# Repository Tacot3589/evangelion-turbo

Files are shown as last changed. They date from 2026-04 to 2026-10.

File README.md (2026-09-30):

# *Big thanks to those who helped make this project possible:*

<p align="center">
  <a href="https://roboilo.com/">
    RoboIlo
  </a>
</p>

<p align="center">
  <a href="https://www.pcbway.com/">
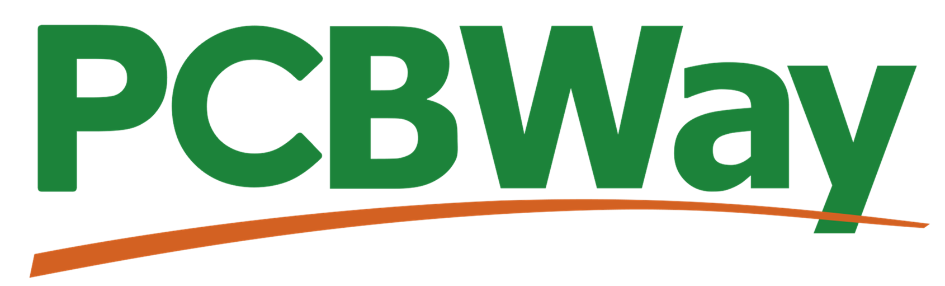
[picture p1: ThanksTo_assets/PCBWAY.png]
PCBWay
    
  </a>
  &nbsp;&nbsp;&nbsp;
  <a href="https://www.rosa3d.pl/en/">
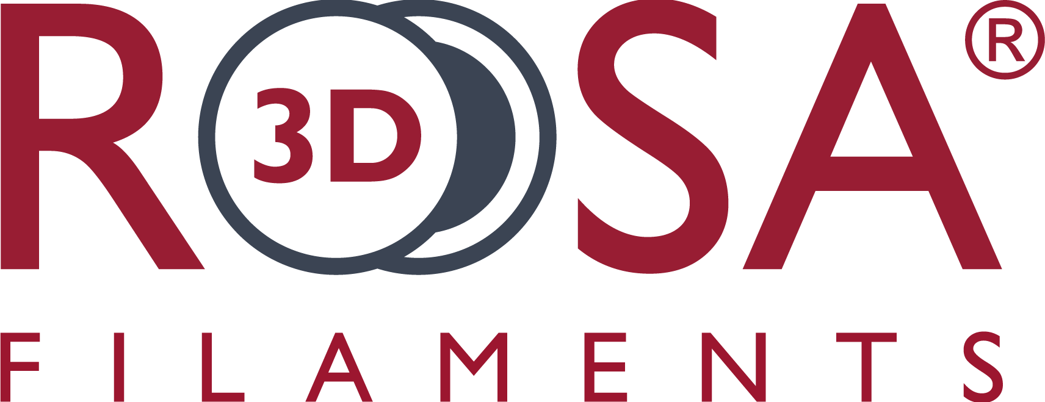
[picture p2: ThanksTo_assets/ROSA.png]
Rosa3D
    
  </a>
</p>

<p align="center">
  <a href="https://forge.hackclub.com/auth/hca/start?ref=7YQKYFS7">
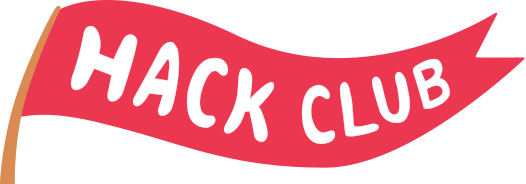
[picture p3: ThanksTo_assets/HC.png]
Hack Club: Forge
    
  </a>
  <a href="https://hackclub.com/">
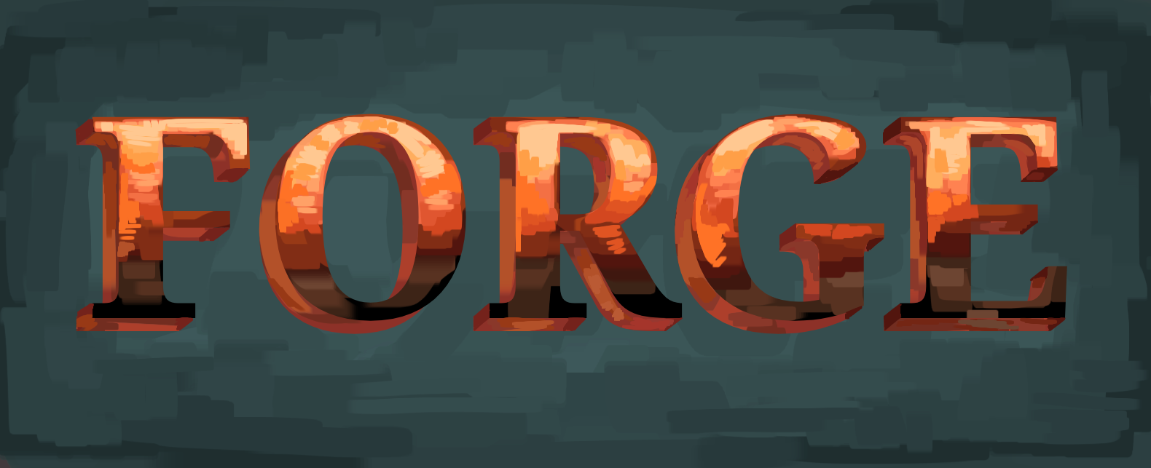
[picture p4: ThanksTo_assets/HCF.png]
Hack Club
    
  </a>
</p>

<p align="center">
  <a href="https://www.omc-stepperonline.com/">
    OMC StepperOnline
  </a>
</p>

---

# Evangelion turbo - my biggest project and most complicated robot yet - succesor to Evangelion
Sumo robot build by me! Designed for RoboRave competition 2026
- 10x10cm robot footprint (max 18-25cm, i think about adding flags)
- max 1kg
- Parts manufactured from steel, aluminium and high performance filaments
- 4 Distance sensors 
- 4 line sensors
- IMU
- shielded motors
- EPROM memory on board
- strong and fast stm32H5 mcu
- 7.5 gear ratio
- powerfull external mosfters motor drivers capable of high current
- two high power brushed DC motors

#### Pros:
 - powerfull motors
 - Capable motors drivers
 - Fast sensors
 - Capable MCU

#### Cons:
 - In the first version, the IMU refused to function (messed up SCL and SDA in I2C)
 - The mighty torque of the motors caused the front to rise, thereby troubling the sensors :(

#### Accomplishments:
 - "RoboRave Robotics Championship 2026 Osaka"

# Photos and images:

## 3D Model:
<p align="center">
  <a>
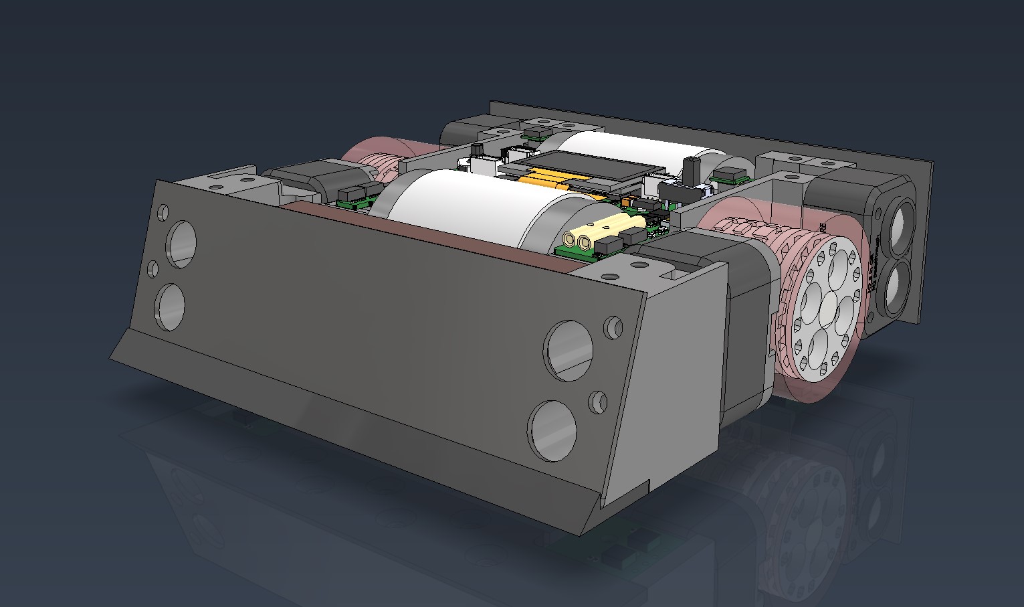
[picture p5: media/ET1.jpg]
ET1
    
  </a>
  <a>
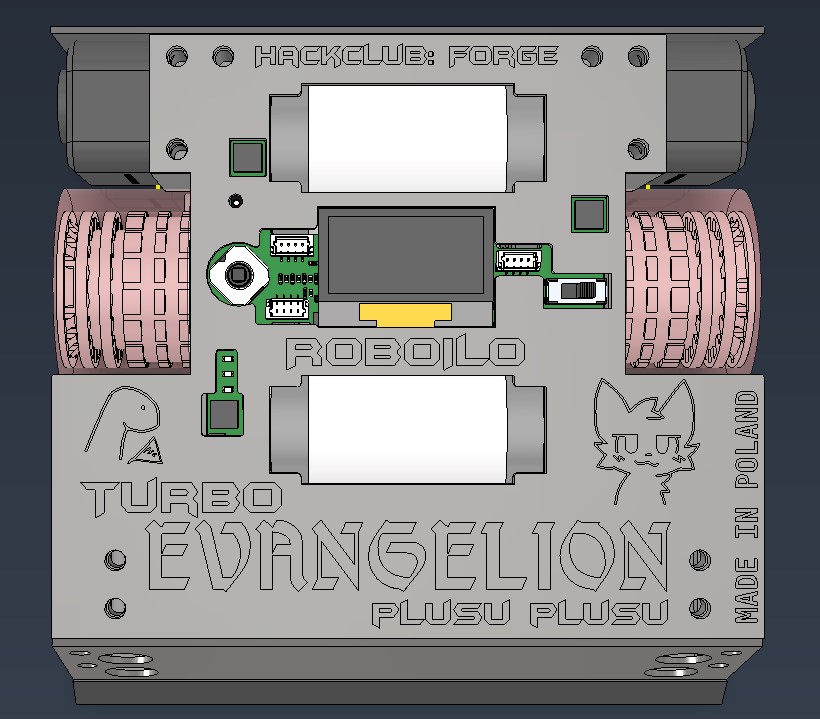
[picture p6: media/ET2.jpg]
ET2
    
  </a>
</p>
<p align="center">
  <a>
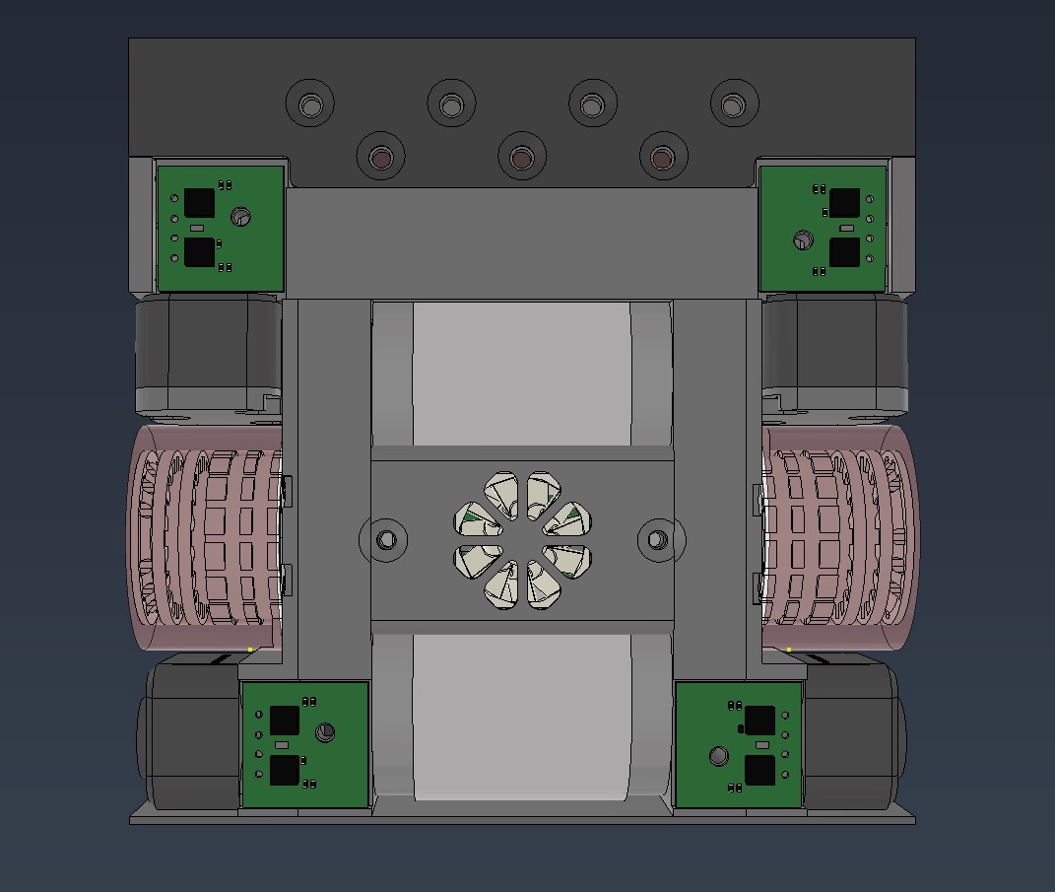
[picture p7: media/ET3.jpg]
ET3
    
  </a>
  <a>
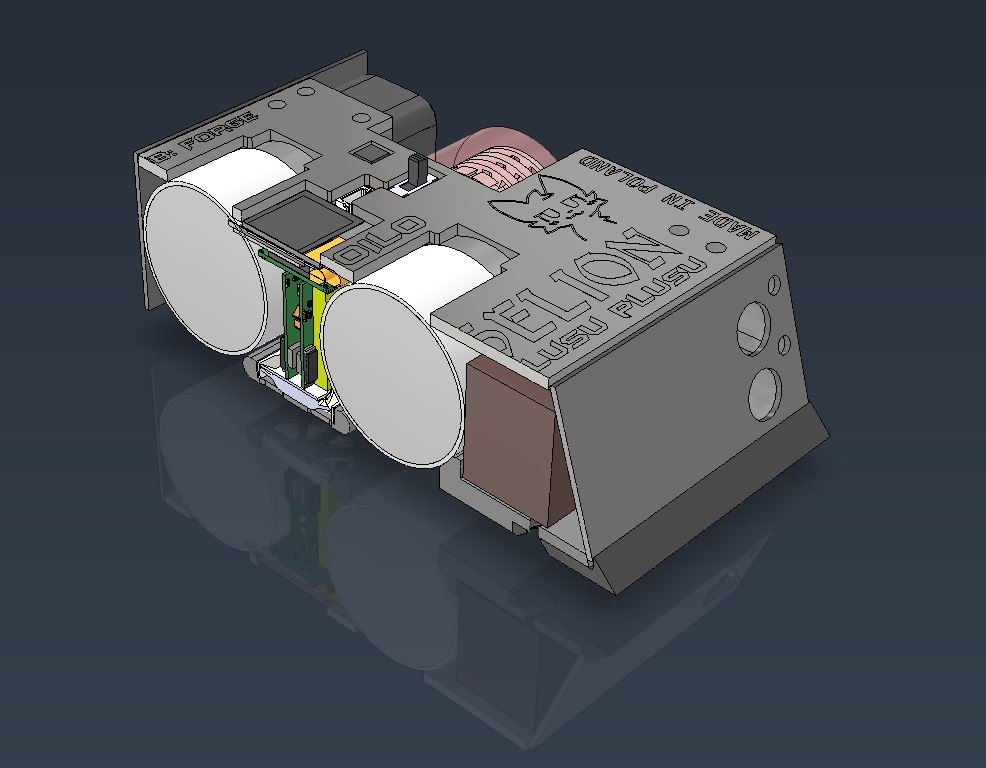
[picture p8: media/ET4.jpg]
ET4
    
  </a>
</p>

## Main controller (4 layer PCB):
<p align="center">
  <a>
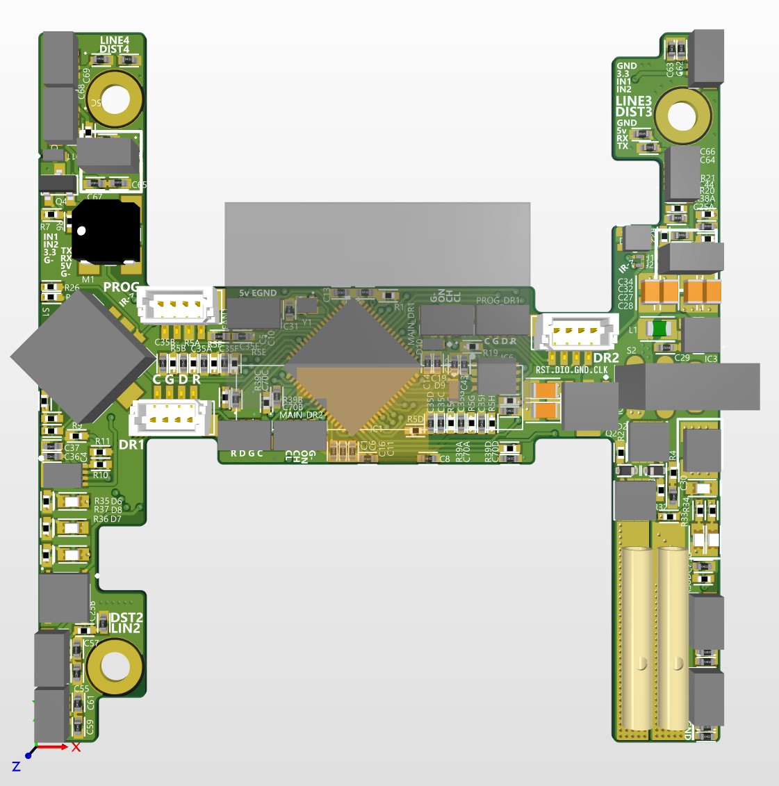
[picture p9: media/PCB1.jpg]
PCB1
    
  </a>
  <a>
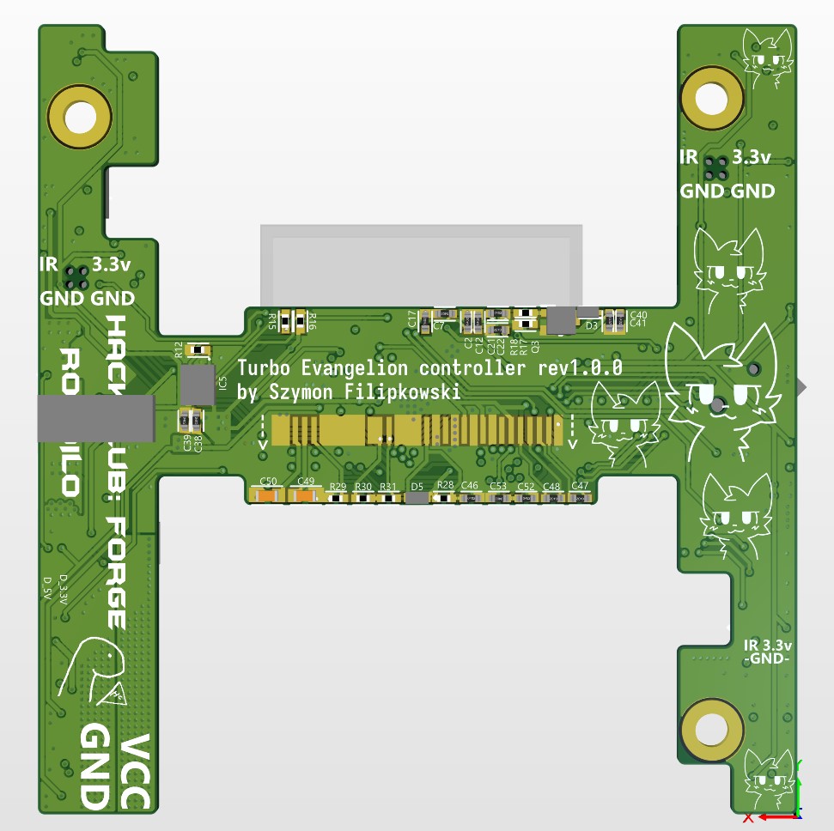
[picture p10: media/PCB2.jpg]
PCB2
    
  </a>
    <a>
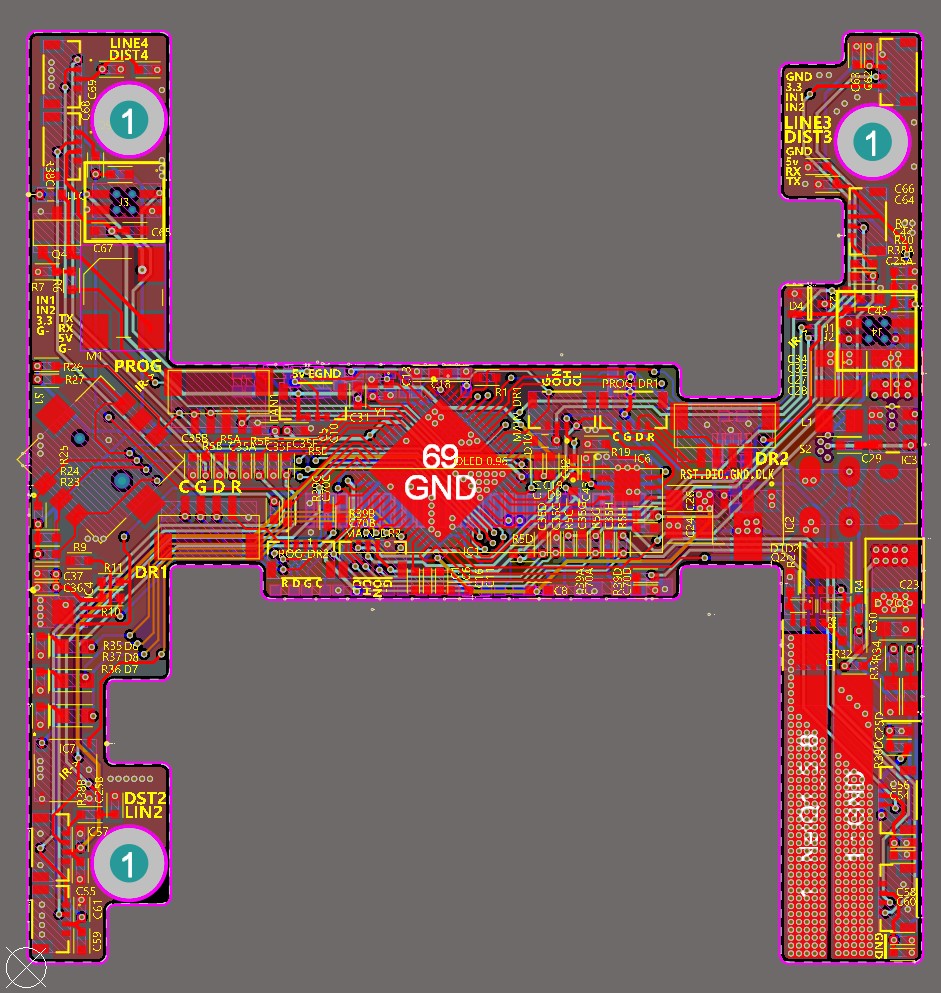
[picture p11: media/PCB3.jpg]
PCB3
    
  </a>
</p>

## Motor driver (4 layer PCB):
<p align="center">
  <a>
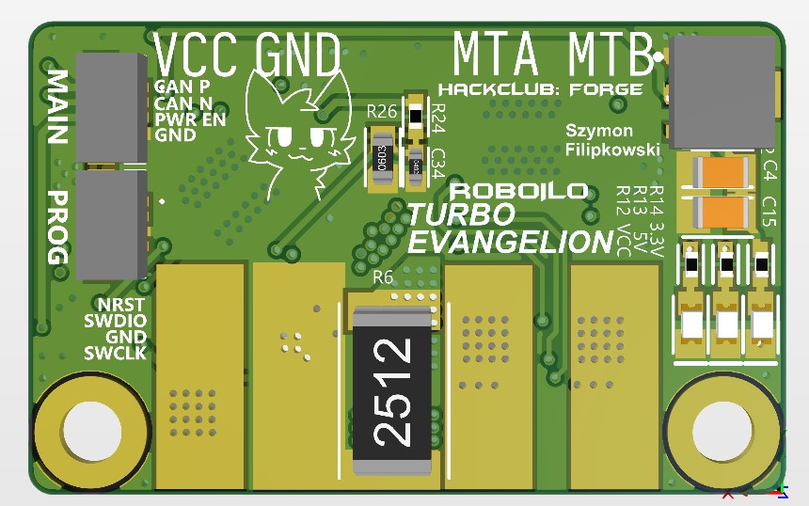
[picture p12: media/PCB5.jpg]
    
  </a>
  <a>
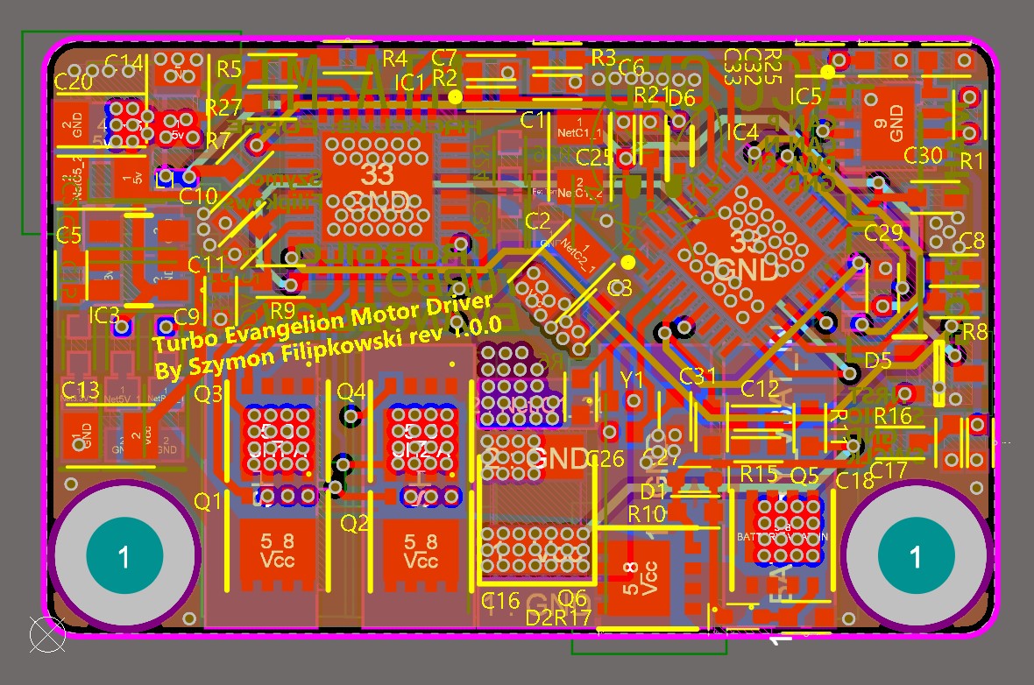
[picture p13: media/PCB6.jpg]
PCB6
    
  </a>
    <a>
    PCB6
  </a>
</p>

## Image of actual robot:
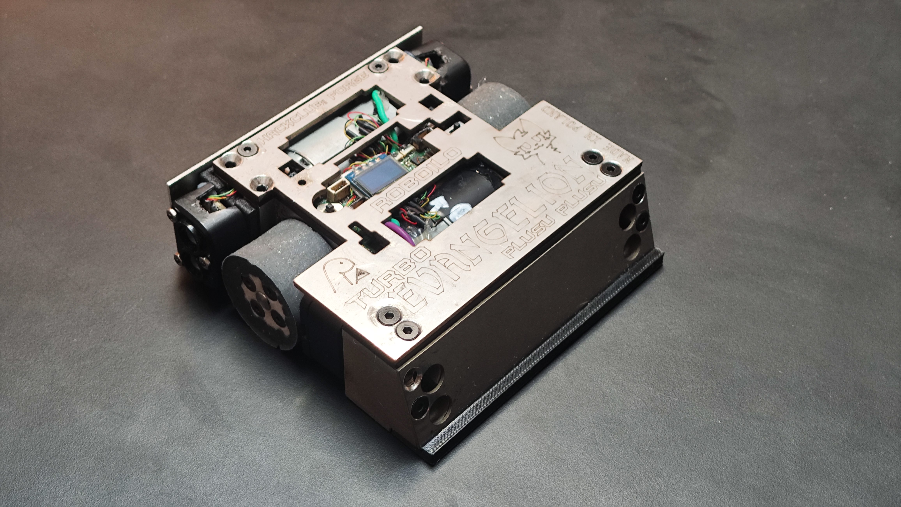
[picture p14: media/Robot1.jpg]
Robot image

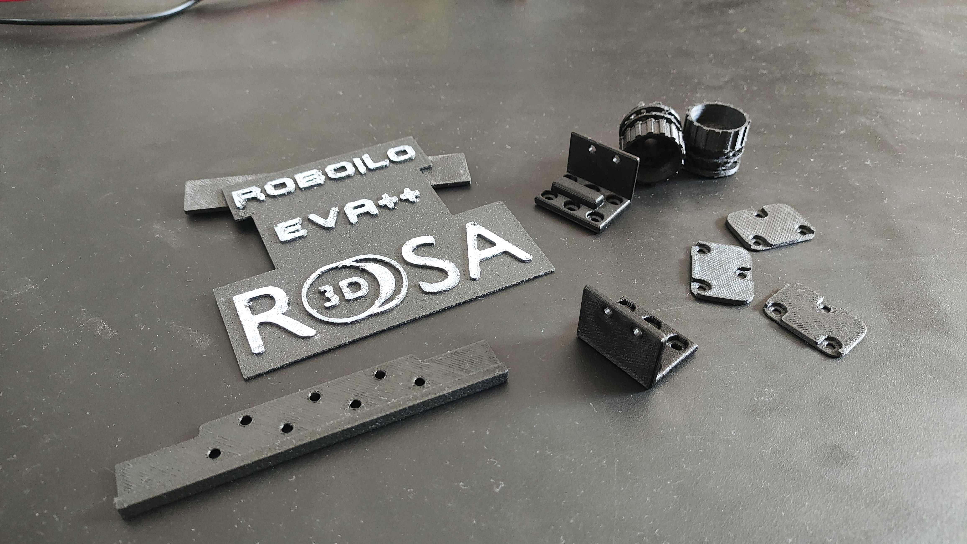
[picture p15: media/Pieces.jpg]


## Prototyping:
<p align="center">
  <a>
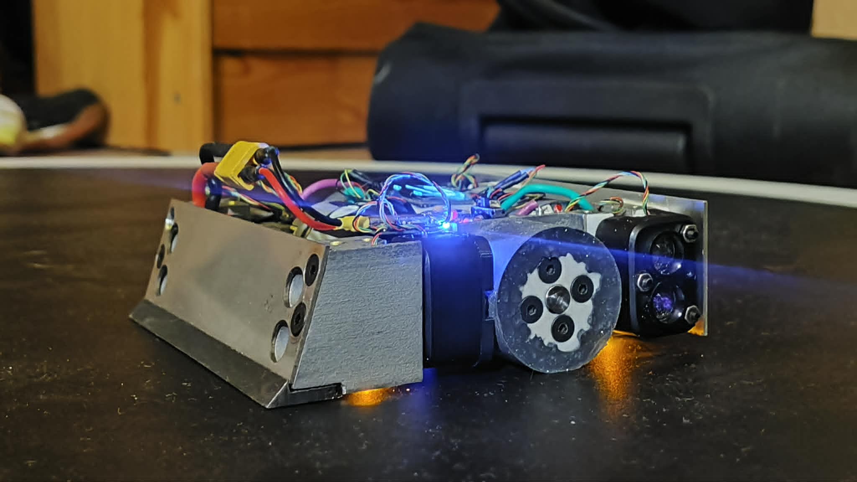
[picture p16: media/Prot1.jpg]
Prototype 1
    
  </a>
  <a>
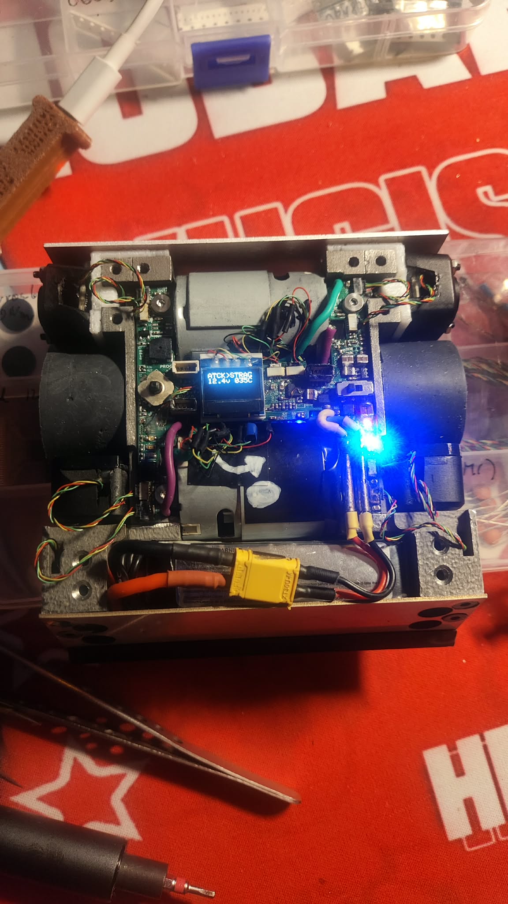
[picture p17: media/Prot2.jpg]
Prototype 2
    
  </a>
</p>

# Rough BOM:
## [Actual BOM](/BOM.csv):
| Name | Quantity |
|---|---|
| RS385 dc motor | 2 |
| pololu 37d 19.4:1 gearboxes | 2 |
| tfluna TOF sensors| 4 |
| main controller PCB | 1 |
| motor driver PCB | 1 |
| rised IR receiver PCB | 2 |
| metal 3D printed parts | *A great many* |
| laser cut 1mm and 2mm parts | 3 |
| CNC cut front wedge | 1 |
| *patience* | *more than a lot* |
| electronical components | *see bom. A lot, lol.* |
| silicone for wheel, shore 10A | 0.5Kg |

## A Most Earnest Plea Unto the Reader
Please - dont copy my work. Watch it, rewiev it, learn from in, take notes - but dont just change a few things and rebuild it. Do better! Make your own better version! Beat me at the next competition!!!*
*This project is out here to **inspire** you, not to be copy and pasted!*

__Fear not. The files are there.__
If you want to take a look:
 - 3D files are in the "3DP" folder
 - Board gerber files are in the "altiumik/*name of the PCB, for example "Riser_IR_receiver_PCB"*/Project Outputs *blah blah blag*" You will find them, dont worry
 - Wiring? Everything is written on the PCBs. If you need more, take a look at the PCB files in "altiumik" folder

## Little insights
### Who am I?
At the time of starting this project, I am a **16-year-old high school student** based in Poland, enrolled in an advanced mathematics, physics, and English program. I am highly active in my school community and our robotics club. My core passions are engineering, robotics, and electronics, and I am aiming to pursue a degree in Electrical Engineering in the future. (**If you represent a university and like my work, feel free to reach out!**). When I step away from the workbench, I love spending my time windsurfing and sailing.
*Constact mail (no spam, please): szymon_fili@proton.me*
### What is it?
It is an miniSUMO robot! 10x10cm max dimensions, 1kg max weight! Battle range is called "dohyo". Most often it is black circle with 5cm white outline - rarely it have inversed colors. Two sumo robots fight! Main target is to push your opponent off the dohyo! Stronger motors, sharper and harder front wedge, faster sensor wins!
In the ./JOURNAL.md file you can check out whole pipeline of designing and building "Turbo Evangelion Plusu Plusu"!
### Why have i build this?
This is my hobby lol! I just likes this! I like electronics, PCB designing, mechanical engineering, material engineering... ALL OF THIS IS SOO COOL!

## Credits
This project uses:
- [Altium Designer](https://www.altium.com/altium-designer) - routing PCB
- [Autodesk inventor](https://www.autodesk.com/products/inventor/overview) - designing all of the parts and assembliess
- [stm32CubeIDE](https://www.st.com/en/development-tools/stm32cubeide.html) - programming the MCU
- [Hack Club Forge](https://forge.hackclub.com/projects/232) - yea, it is my project :)

## First competition of this robot!
<p align="center">
  <a href="https://roborave-osaka.org/wc2026_en/">
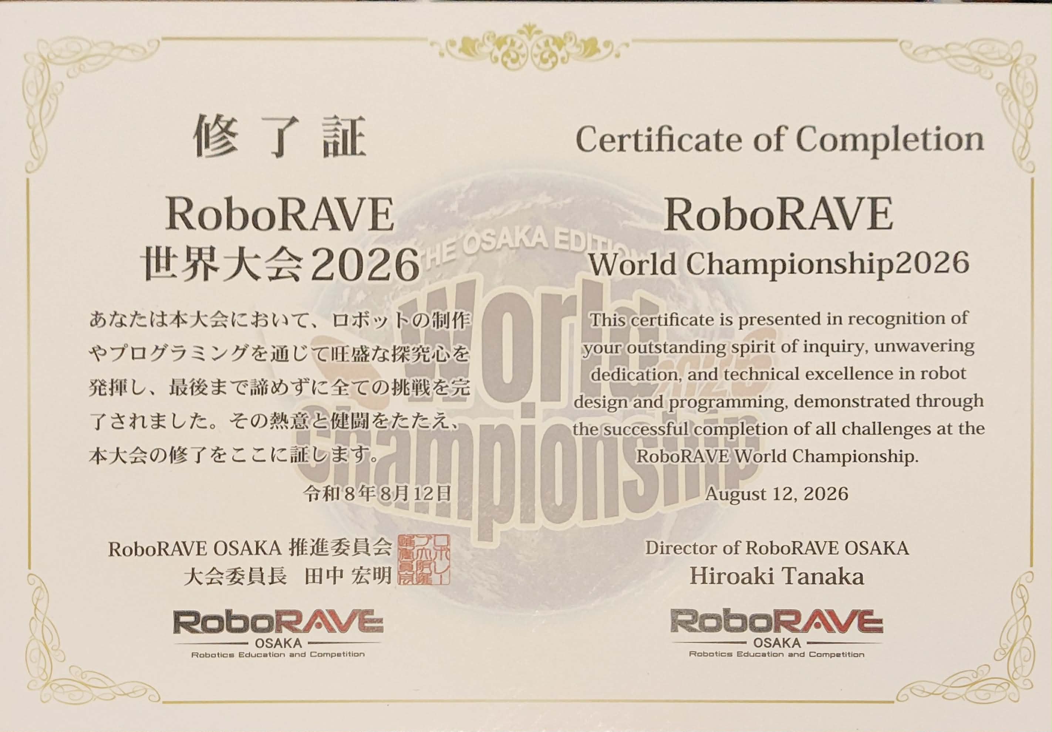
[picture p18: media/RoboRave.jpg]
    
  </a>
</p>

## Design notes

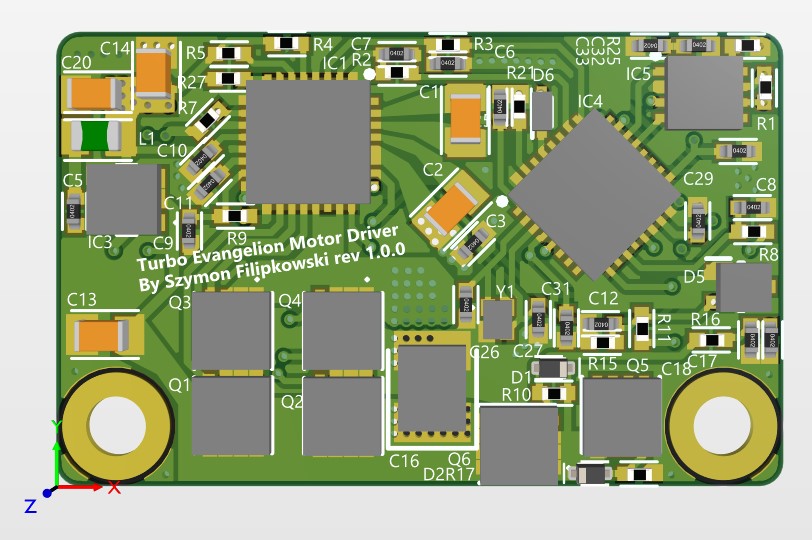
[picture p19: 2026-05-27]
media/PCB4.jpg

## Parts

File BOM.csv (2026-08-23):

Comment | Description | Designator | Footprint | LibRef | Quantity | Example part link (major components only)
A looot of 3D printer parts | Preferably metal 3D printed |  |  |  | 1 | Order by yourself, for example, via PCBWay
Front wedge blackened | as hard as you can. CNC steel + blackening |  |  |  | 1 | Order by yourself, for example, via PCBWay
steel Front and back - 1mm | laser cutting |  |  |  | 1 | Order by yourself, for example, via PCBWay
Ceiling - 2mm steel | added cute laser marks :) |  |  |  | 1 | Order by yourself, for example, via PCBWay
4 layer PCB - main controller |  |  |  |  | 1 | Order by yourself, for example, via PCBWay
4 layer PCB - motor driver |  |  |  |  | 2 | Order by yourself, for example, via PCBWay
2 layer PCB - ir receiver |  |  |  |  | 1 | Order by yourself, for example, via PCBWay
2 layer PCB - line sensors |  |  |  |  | 4 | Order by yourself, for example, via PCBWay
A looooot of M3 M2.5 M2 screws | get a kit - will be cheaper lol |  |  |  | 1 | Order by yourself, Aliexpres is pretty good and cheap for this stuff. Amazon also works
Silicone shore 10A - 0.5Kg | for squishy and grippy wheeeeels |  |  |  | 1 | Like any silicone, rubber or latex will work, lol. Get one from Amazon
lipo 3s 450mAh battery | get it goin! |  |  |  | 2 | https://www.racedayquads.com/products/tattu-450mah-3s-75c-lipo-battery-xt30-long-type
pololu 37D with 19.4:1 gearboxes | you can get knockoffs from ali cheaper |  |  |  | 2 | https://www.pololu.com/product/4741
some RS380 dc motors | to power everything up |  |  |  | 2 | https://www.aliexpress.com/item/1005012061086477.html?curPageLogUid=sVZiq3anDUVm
Tfluna tof sensors | quick tof sensors - about 30 buck per piece |  |  |  | 4 | https://www.amazon.com/Benewake-TF-Luna-Ranging-Compatible-Raspberry/dp/B0DKCSF8C5
Patience | priceless |  |  |  | 1 | A looot
STM32 st-link v2 | it costs about 3 bucks on ali - get one to program this thing |  |  |  | 1 | https://www.aliexpress.com/item/1005009246421297.html?curPageLogUid=WTBzfEx3DPnn
TSOP57438TT1 | Integrated Circuit | IC1 | TSOP57438TT1 | TSOP57438TT1 | 1 | Get it from your nearest microcomponents seller. Ex. DigiKey, mouser, ls componenc, farnell…
FTM-102-02-L-DV | Connector | J1 | FTM-102-XX-Y-DV | FTM-102-02-L-DV | 1 | Get it from your nearest microcomponents seller. Ex. DigiKey, mouser, ls componenc, farnell…
1uF | MLCC Capacitor | C1 C2 C5 C6 C7 C13 C14 C30 C36 C38 C40 C42 C44 C45 C46 C47 C48 C52 C54 C55 C58 C59 C62 C64 C65 C68 | C 0402 | Capacitor | 26 | Get it from your nearest microcomponents seller. Ex. DigiKey, mouser, ls componenc, farnell…
100nF | MLCC Capacitor | C8 C10 C11 C12 C16 C17 C18 C19 C29 C31 C35A C35B C35C C35D C35E C35F C35G C35H C37 C39 C41 C43 C53 C56 C57 C60 C61 C63 C66 C67 C69 | C 0402 | Capacitor | 31 | Get it from your nearest microcomponents seller. Ex. DigiKey, mouser, ls componenc, farnell…
10pF | MLCC Capacitor | C21 C22 C25A C25B C25C C25D C70A C70B C70C C70D | C 0402 | Capacitor | 10 | Get it from your nearest microcomponents seller. Ex. DigiKey, mouser, ls componenc, farnell…
TL8B0336M020C (33uF tantalum cap) | Capacitor Polarised | C23 | CAPPC3528X100N | TL8B0336M020C | 1 | Get it from your nearest microcomponents seller. Ex. DigiKey, mouser, ls componenc, farnell…
22uF | MLCC Capacitor | C24 | C 0805 | Capacitor | 1 | Get it from your nearest microcomponents seller. Ex. DigiKey, mouser, ls componenc, farnell…
10uF | MLCC Capacitor | C26 | C 0805 | Capacitor | 1 | Get it from your nearest microcomponents seller. Ex. DigiKey, mouser, ls componenc, farnell…
22uF 16V | MLCC Capacitor | C27 C32 | C 0805 | Capacitor | 2 | Get it from your nearest microcomponents seller. Ex. DigiKey, mouser, ls componenc, farnell…
10uF 16v | MLCC Capacitor | C28 C34 | C 0805 | Capacitor | 2 | Get it from your nearest microcomponents seller. Ex. DigiKey, mouser, ls componenc, farnell…
2.2uF | MLCC Capacitor | C49 | C 0603 | Capacitor | 1 | Get it from your nearest microcomponents seller. Ex. DigiKey, mouser, ls componenc, farnell…
4.7uF | MLCC Capacitor | C50 | C 0603 | Capacitor | 1 | Get it from your nearest microcomponents seller. Ex. DigiKey, mouser, ls componenc, farnell…
 | Zener Diode sod523 | D1 D2 | SOD523 | BZX585 | 2 | Get it from your nearest microcomponents seller. Ex. DigiKey, mouser, ls componenc, farnell…
BAS5202VH6327XTSA1 | Schottky Diode | D3 | SODFL1608X59N | BAS5202VH6327XTSA1 | 1 | Get it from your nearest microcomponents seller. Ex. DigiKey, mouser, ls componenc, farnell…
BAV199W-7 | Diode | D4 | SOT65P210X110-3N | BAV199W-7 | 1 | Get it from your nearest microcomponents seller. Ex. DigiKey, mouser, ls componenc, farnell…
1N4148WT-7 | Diode | D5 D9 D10 D11 | 1N4148WT7 | 1N4148WT-7 | 4 | Get it from your nearest microcomponents seller. Ex. DigiKey, mouser, ls componenc, farnell…
LED BLUE |  | D6 D_5V | LED 0603 BLUE | LED BLUE | 2 | Get it from your nearest microcomponents seller. Ex. DigiKey, mouser, ls componenc, farnell…
LED RED |  | D7 D_VCC | LED 0603 RED | LED RED | 2 | Get it from your nearest microcomponents seller. Ex. DigiKey, mouser, ls componenc, farnell…
LED GREEN |  | D8 D_3.3V | LED 0603 GREEN | LED GREEN | 2 | Get it from your nearest microcomponents seller. Ex. DigiKey, mouser, ls componenc, farnell…
DF53-4S-0.6H | Connector | DIST1 DIST3 DIST4 DST2 FAN1 LIN2 LINE1 LINE3 LINE4 MAIN_DR1 MAIN_DR2 PROG_DR1 PROG_DR2 | DF534S06H | DF53-4S-0.6H | 13 | Get it from your nearest microcomponents seller. Ex. DigiKey, mouser, ls componenc, farnell…
4 PIN |  | DR1 DR2 PROG | BM04B-SRSS-TB | 4 PIN | 3 | Get it from your nearest microcomponents seller. Ex. DigiKey, mouser, ls componenc, farnell…
banana_plug | banana plug for high current scenarios | GND VCC | Banana plug 2mm-smol | banana_plug | 2 | Aliexpress or amazon guys
STM32H562RIV6 | Integrated Circuit | IC1 | QFN40P800X800X100-69N-D | STM32H562RIV6 | 1 | Get it from your nearest microcomponents seller. Ex. DigiKey, mouser, ls componenc, farnell…
AZ1117CR2-3.3TRG1 | Integrated Circuit | IC2 | AZ1117CR33TRG1 | AZ1117CR2-3.3TRG1 | 1 | Get it from your nearest microcomponents seller. Ex. DigiKey, mouser, ls componenc, farnell…
AP63203WU-7 | Integrated Circuit | IC3 | AP63203WU7 | AP63203WU-7 | 1 | Get it from your nearest microcomponents seller. Ex. DigiKey, mouser, ls componenc, farnell…
AT24C02D-MAHM-E | Integrated Circuit | IC4 | SON50P300X200X60-9N | AT24C02D-MAHM-E | 1 | Get it from your nearest microcomponents seller. Ex. DigiKey, mouser, ls componenc, farnell…
LSM6DSV320XTR | Integrated Circuit | IC5 | LSM6DSV16BXTR | LSM6DSV320XTR | 1 | Get it from your nearest microcomponents seller. Ex. DigiKey, mouser, ls componenc, farnell…
TCAN1042VDRBTQ1 | Integrated Circuit | IC6 | SON65P300X300X100-9N-D | TCAN1042VDRBTQ1 | 1 | Get it from your nearest microcomponents seller. Ex. DigiKey, mouser, ls componenc, farnell…
TSOP57438TT1 | Integrated Circuit | IC7 | TSOP57438TT1 | TSOP57438TT1 | 1 | Get it from your nearest microcomponents seller. Ex. DigiKey, mouser, ls componenc, farnell…
NOPE | Resistor | J1 J2 | ERJ1GNF1000C | ERJ1GNJ103C | 2
MLE-102-01-G-DV | Connector | J3 J4 | MLE10201GDV - ir receiver | MLE-102-01-G-DV | 2 | Get it from your nearest microcomponents seller. Ex. DigiKey, mouser, ls componenc, farnell…
22uH | General pourpouse inductor | L1 | L 0805 | Inductor | 1 | Get it from your nearest microcomponents seller. Ex. DigiKey, mouser, ls componenc, farnell…
Buzzer |  | M1 | HCT5020A | HCT5020A | 1 | Get it from your nearest microcomponents seller. Ex. DigiKey, mouser, ls componenc, farnell…
oled flex 0.96 |  | OLED1 | oled flex 0.96 | oled flex 0.96 | 1 | https://www.aliexpress.com/item/1005012808166804.html?curPageLogUid=72tuneL2vCGw
P mos power |  | Q1 Q2 | dfn33 | P mos power | 2 | Get it from your nearest microcomponents seller. Ex. DigiKey, mouser, ls componenc, farnell…
Model | General Pourpouse Mosfet | Q3 | SOT323 | N Mosfet | 1 | Get it from your nearest microcomponents seller. Ex. DigiKey, mouser, ls componenc, farnell…
Model | General Pourpouse Mosfet | Q4 | SOT23-3 | N Mosfet | 1 | Get it from your nearest microcomponents seller. Ex. DigiKey, mouser, ls componenc, farnell…
10k | General pourpouse resistor | R1 R2 R4 R7 R9 R12 R17 R19 R21 R23 R24 R25 R26 R27 R32 | R 0402 | Resistor | 15 | Get it from your nearest microcomponents seller. Ex. DigiKey, mouser, ls componenc, farnell…
47K | General pourpouse resistor | R3 | R 0402 | Resistor | 1 | Get it from your nearest microcomponents seller. Ex. DigiKey, mouser, ls componenc, farnell…
1K | General pourpouse resistor | R5A R5B R5C R5D R5E R5F R5G R5H R22 R34 | R 0402 | Resistor | 10 | Get it from your nearest microcomponents seller. Ex. DigiKey, mouser, ls componenc, farnell…
470R | General pourpouse resistor | R6 | R 0402 | Resistor | 1 | Get it from your nearest microcomponents seller. Ex. DigiKey, mouser, ls componenc, farnell…
4.7K | General pourpouse resistor | R10 R11 R15 R16 | R 0402 | Resistor | 4 | Get it from your nearest microcomponents seller. Ex. DigiKey, mouser, ls componenc, farnell…
330R | General pourpouse resistor | R18 R35 R36 R37 | R 0402 | Resistor | 4 | Get it from your nearest microcomponents seller. Ex. DigiKey, mouser, ls componenc, farnell…
91k | General pourpouse resistor | R20 | R 0402 | Resistor | 1 | Get it from your nearest microcomponents seller. Ex. DigiKey, mouser, ls componenc, farnell…
4K7 | General pourpouse resistor | R28 R30 R31 | R 0402 | Resistor | 3 | Get it from your nearest microcomponents seller. Ex. DigiKey, mouser, ls componenc, farnell…
390K | General pourpouse resistor | R29 | R 0402 | Resistor | 1 | Get it from your nearest microcomponents seller. Ex. DigiKey, mouser, ls componenc, farnell…
2.1K | General pourpouse resistor | R33 | R 0402 | Resistor | 1 | Get it from your nearest microcomponents seller. Ex. DigiKey, mouser, ls componenc, farnell…
30R | General pourpouse resistor | R38A R38B R38C R38D R39A R39B R39C R39D | R 0402 | Resistor | 8 | Get it from your nearest microcomponents seller. Ex. DigiKey, mouser, ls componenc, farnell…
SKRHABE010 | Switch | S1 | SKRHABE010 | SKRHABE010 | 1 | Get it from your nearest microcomponents seller. Ex. DigiKey, mouser, ls componenc, farnell…
EG1271A | Switch | S2 | EG1271 | EG1271A | 1 | Get it from your nearest microcomponents seller. Ex. DigiKey, mouser, ls componenc, farnell…
US3200005Z | Crystal or Oscillator | Y1 | US3200005Z | US3200005Z | 1 | Get it from your nearest microcomponents seller. Ex. DigiKey, mouser, ls componenc, farnell…
LED GREEN |  | 3.3V | LED 0603 GREEN | LED GREEN | 2 | Get it from your nearest microcomponents seller. Ex. DigiKey, mouser, ls componenc, farnell…
LED BLUE |  | 5V | LED 0603 BLUE | LED BLUE | 2 | Get it from your nearest microcomponents seller. Ex. DigiKey, mouser, ls componenc, farnell…
100nF 100V | MLCC Capacitor | C1 | C 0805 | Capacitor | 2 | Get it from your nearest microcomponents seller. Ex. DigiKey, mouser, ls componenc, farnell…
1uF 50V | MLCC Capacitor | C2 | C 0805 | Capacitor | 2 | Get it from your nearest microcomponents seller. Ex. DigiKey, mouser, ls componenc, farnell…
100nF 50V | MLCC Capacitor | C3 | C 0402 | Capacitor | 2 | Get it from your nearest microcomponents seller. Ex. DigiKey, mouser, ls componenc, farnell…
22uF | MLCC Capacitor | C4 | C 0805 | Capacitor | 2 | Get it from your nearest microcomponents seller. Ex. DigiKey, mouser, ls componenc, farnell…
100nF | MLCC Capacitor | C5 C18 C25 C29 C30 C33 | C 0402 | Capacitor | 12 | Get it from your nearest microcomponents seller. Ex. DigiKey, mouser, ls componenc, farnell…
10pF | MLCC Capacitor | C6 C7 C9 C26 C27 | C 0402 | Capacitor | 10 | Get it from your nearest microcomponents seller. Ex. DigiKey, mouser, ls componenc, farnell…
1nF | MLCC Capacitor | C8 | C 0402 | Capacitor | 2 | Get it from your nearest microcomponents seller. Ex. DigiKey, mouser, ls componenc, farnell…
1uF | MLCC Capacitor | C10 C11 C12 C17 C31 C32 C34 | C 0402 | Capacitor | 14 | Get it from your nearest microcomponents seller. Ex. DigiKey, mouser, ls componenc, farnell…
10uF 16v | MLCC Capacitor | C13 | C 0805 | Capacitor | 2 | Get it from your nearest microcomponents seller. Ex. DigiKey, mouser, ls componenc, farnell…
22uF 16V | MLCC Capacitor | C14 C20 | C 0805 | Capacitor | 4 | Get it from your nearest microcomponents seller. Ex. DigiKey, mouser, ls componenc, farnell…
10uF | MLCC Capacitor | C15 | C 0805 | Capacitor | 2 | Get it from your nearest microcomponents seller. Ex. DigiKey, mouser, ls componenc, farnell…
TL8B0336M020C (33uF tantalum cap) | Capacitor Polarised | C16 | CAPPC3528X100N | TL8B0336M020C | 2 | Get it from your nearest microcomponents seller. Ex. DigiKey, mouser, ls componenc, farnell…
 | Zener Diode sod523 | D1 D2 | SOD523 | BZX585 | 4 | Get it from your nearest microcomponents seller. Ex. DigiKey, mouser, ls componenc, farnell…
BAV199W-7 | Diode | D5 | SOT65P210X110-3N | BAV199W-7 | 2 | Get it from your nearest microcomponents seller. Ex. DigiKey, mouser, ls componenc, farnell…
BAS5202VH6327XTSA1 | Schottky Diode | D6 | SODFL1608X59N | BAS5202VH6327XTSA1 | 2 | Get it from your nearest microcomponents seller. Ex. DigiKey, mouser, ls componenc, farnell…
banana_plug | banana plug for high current scenarios | GND MTA MTB VCC | Banana plug 3mm half | banana_plug | 8 | Aliexpress or amazon guys
DRV8702QRHBRQ1 | Integrated Circuit | IC1 | QFN50P500X500X90-33N-D | DRV8702QRHBRQ1 | 2 | Get it from your nearest microcomponents seller. Ex. DigiKey, mouser, ls componenc, farnell…
AZ1117CR2-3.3TRG1 | Integrated Circuit | IC2 | AZ1117CR33TRG1 | AZ1117CR2-3.3TRG1 | 2 | Get it from your nearest microcomponents seller. Ex. DigiKey, mouser, ls componenc, farnell…
AP63203WU-7 | Integrated Circuit | IC3 | AP63203WU7 | AP63203WU-7 | 2 | Get it from your nearest microcomponents seller. Ex. DigiKey, mouser, ls componenc, farnell…
STM32G431K6U3 | Integrated Circuit | IC4 | QFN50P500X500X60-33N-D | STM32G431K6U3 | 2 | Get it from your nearest microcomponents seller. Ex. DigiKey, mouser, ls componenc, farnell…
TCAN1042VDRBTQ1 | Integrated Circuit | IC5 | SON65P300X300X100-9N-D | TCAN1042VDRBTQ1 | 2 | Get it from your nearest microcomponents seller. Ex. DigiKey, mouser, ls componenc, farnell…
22uH | General pourpouse inductor | L1 | L 0805 | Inductor | 2 | Get it from your nearest microcomponents seller. Ex. DigiKey, mouser, ls componenc, farnell…
DF53-4S-0.6H | Connector | MAIN PROG | DF534S06H | DF53-4S-0.6H | 4 | Get it from your nearest microcomponents seller. Ex. DigiKey, mouser, ls componenc, farnell…
N mos power | N-Mosfet DFN 5x6 | Q1 Q2 Q3 Q4 | DFN33 | Power MOSFET | 8 | Get it from your nearest microcomponents seller. Ex. DigiKey, mouser, ls componenc, farnell…
P mos power |  | Q5 Q6 | dfn33 | P mos power | 4 | Get it from your nearest microcomponents seller. Ex. DigiKey, mouser, ls componenc, farnell…
120R | General pourpouse resistor | R1 | R 0402 | Resistor | 2 | Get it from your nearest microcomponents seller. Ex. DigiKey, mouser, ls componenc, farnell…
1k | General pourpouse resistor | R2 R3 R14 | R 0402 | Resistor | 6 | Get it from your nearest microcomponents seller. Ex. DigiKey, mouser, ls componenc, farnell…
470R | General pourpouse resistor | R4 R5 | R 0402 | Resistor | 4 | Get it from your nearest microcomponents seller. Ex. DigiKey, mouser, ls componenc, farnell…
20mR | General pourpouse resistor | R6 | R 2512 | Resistor | 2 | Get it from your nearest microcomponents seller. Ex. DigiKey, mouser, ls componenc, farnell…
10k | General pourpouse resistor | R7 R8 R9 R12 R15 R16 R17 R24 R25 R27 | R 0402 | Resistor | 20 | Get it from your nearest microcomponents seller. Ex. DigiKey, mouser, ls componenc, farnell…
47K | General pourpouse resistor | R10 | R 0402 | Resistor | 2 | Get it from your nearest microcomponents seller. Ex. DigiKey, mouser, ls componenc, farnell…
91k | General pourpouse resistor | R11 | R 0402 | Resistor | 2 | Get it from your nearest microcomponents seller. Ex. DigiKey, mouser, ls componenc, farnell…
2.1K | General pourpouse resistor | R13 | R 0402 | Resistor | 2 | Get it from your nearest microcomponents seller. Ex. DigiKey, mouser, ls componenc, farnell…
100k | General pourpouse resistor | R21 | R 0402 | Resistor | 2 | Get it from your nearest microcomponents seller. Ex. DigiKey, mouser, ls componenc, farnell…
NTC 10k | General pourpouse resistor | R26 | R 0603 | Resistor | 2 | Get it from your nearest microcomponents seller. Ex. DigiKey, mouser, ls componenc, farnell…
LED RED |  | VCC | LED 0603 RED | LED RED | 2 | Get it from your nearest microcomponents seller. Ex. DigiKey, mouser, ls componenc, farnell…
US3200005Z | Crystal or Oscillator | Y1 | US3200005Z | US3200005Z | 2 | Get it from your nearest microcomponents seller. Ex. DigiKey, mouser, ls componenc, farnell…
1M/1000K/as big as you can find | Breadboard resistor |  |  |  | 5 | Get it from your nearest microcomponents seller. Ex. DigiKey, mouser, ls componenc, farnell…
100nF/1uF | Breadboard capacitor mlcc |  |  |  | 5 | Get it from your nearest microcomponents seller. Ex. DigiKey, mouser, ls componenc, farnell…

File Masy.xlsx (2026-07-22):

Nazwa | Masa [g] | Ilosc | Ilość 2
Koło | 15.00 | 2 | 2
Felga SLS biała | 2.90 | 0 | 0
Uchwyt wewnętrzny na łożysko igiełkowe, SLS | 0.70 | 2 | 2
Obódowa LUNA | 2.28 | 4 | 4
Uchwyt LUNA, tylny | 1.45 | 2 | 2
Silnik | 86.00 | 2 | 2
PCB LUNA | 1.50 | 4 | 4
dach stal | 74.00 | 1 | 0
Przód aluminiowy | 6.40 | 0 | 1
Przód stalowy | 17.33 | 1 | 0
Tył aluminiowy | 7.72 | 1 | 1
Płóg stal #45 | 30.00 | 0 | 0
Płóg stal S7 | 26.00 | 1 | 1
Huby stalowe | 14.00 | 2 | 2
Wewnętrzny uchwyt na PCB, SLS | 2.25 | 1 | 1
Front mount, SLS | 15.80 | 0 | 1
Front mount, stal | 136.00 | 1 | 0
Left gearbox cover, SLS | 4.10 | 0 | 1
Left gearbox cover, stal | 39.00 | 1 | 0
Right gearbox cover, SLS | 4.10 | 0 | 1
Right gearbox cover, stal | 39.00 | 1 | 0
Left gearbox, SLS | 8.10 | 0 | 1
Left gearbox, stal | 70.50 | 1 | 0
Right gearbox, SLS | 8.10 | 0 | 1
Right gearbox, stal | 70.50 | 1 | 0
Line sensor | 1.00 | 4 | 4
Łożysko igiełkowe, wewnętrzne | 1.65 | 2 | 2
Zębatka z ośką | 10.80 | 2 | 2
Zębatka pośrednia | 3.30 | 2 | 2
Łożysko kulkowe flange, zewnętrzne | 0.80 | 2 | 2
Ośka do łożyska pośredniego 2mm | 0.50 | 2 | 2
Lipo 3s 450mAh | 39.00 | 0 | 0
Lipo 3S 300mAh | 22.50 | 1 | 1
Śruby, kabelki, elektronika | 53.00 | 1 | 1
RAZEM: |  | 845.32 | 445.59

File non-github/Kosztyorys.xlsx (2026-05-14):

What | Cost in PLN | Cost in USD | Where to buy | Comment (if needed) | PLN to USD conversion rate
screws m3x4mm buttonhead | 5.05 | 1.39 | Aliexpress | for mounting metal front | 3.6410
screws m2x16mm buttonhead | 5.79 | 1.59 | Aliexpress | for mounting distance sensors
screws m3x5 countersunk | 6.91 | 1.90 | Aliexpress | for sharp from | Sum in USD: | 792.45
banana plug 2mm pair 10pcs | 7.89 | 2.17 | Aliexpress | for motors and main power | Sum in PLN: | 2921.70
0.96inch flex oled 3pcs | 19.77 | 5.43 | Aliexpress | electronic parts have tendencies to burn easily
m2.5 thin nut 50pcs | 3.35 | 0.92 | Aliexpress | to secure PCBs
needle bearing HK0607 6x10x7mm | 14.49 | 3.98 | Aliexpress | wheeeeeeee… i love when it is efficient
flange bearing 6x10x3mm | 18.51 | 5.08 | Aliexpress | wheeeeeeee… i love when it is efficient
two pololu 37d gearboxes 19:1 | 44.82 | 12.31 | Aliexpress | knockoff from ali, its hella cheaper - i have used similiar in my previous robot
10t 2.28 0.5M brass gear for motor | 14.78 | 4.06 | Aliexpress | gearboxes
screws M2.5x8mm flathead | 5.68 | 1.56 | Aliexpress | for mounting line sensors
grub screws m3x5mm | 5.00 | 1.37 | Aliexpress | for mounting wheels
screws M2.5x6mm flathead | 5.44 | 1.49 | Aliexpress | for mounting PCBs
m2.5x6x0.1mm washer | 7.14 | 1.96 | Aliexpress | to make gearboxes slide easier
RS-385 dc motor 3 pcs | 45.96 | 12.62 | Aliexpress | 3psc of dc motors (one more, beacuse it will burn i am worried)
1mm sturdy metal front - laser cut | 30.00 | 8.24 | Lasercut locally | i found cheap offer locally
1mm sturdy metal back - laser cut | 30.00 | 8.24 | Lasercut locally | i found cheap offer locally
2mm metal ceil - laser cut | 30.00 | 8.24 | Lasercut locally | i found cheap offer locally
PCBs 4 layer | 100.00 | 27.46 | JLC | 2 motors 1 controller
MJF gearboxes - 1kg weight class | 220.00 | 60.42 | JLC | gearboxes, mounts
MJF wheel hubs | 54.62 | 15.00 | JLC | for wheels and axes
Nylon SLS gearboxes - 0.5kg weight class | 29.13 | 8.00 | JLC | Moer lightweight but less rigid
Nylon SLS rims for wheels | 14.56 | 4.00 | JLC | Whellie wheels
other Nylon SLS parts, PCB holder etc | 14.56 | 4.00 | JLC | motor drivers pcb holder, bearings holder
MJF steel front part | 143.64 | 39.45 | JLC | as sturdy as one could get
CNC front plow/wedge, steel alloy, blackening. I recommend 2 pcc | 280.00 | 76.90 | JLC | one may go dull at the competition. A sumo robot with dull plow is a robot who already lost…
JCL shipping | 54.62 | 15.00 | JLC | i dont know, but i think it will be not-so-cheap type of shipping
JLC -10 bucks cupon | 0.00 | -10.00 | JLC | I wanted to include it lol
silicone shore 10A for wheels | 50.00 | 13.73 | Allegro (polish marketplace) | good silicone wheels
M3, M2.5, M2 tap | 45.00 | 12.36 | Aliexpress | Tapping via JCL i like adding a lot of money
Fan for cooling (yup. In the robot) 2pcs | 50.00 | 13.73 | Aliexpress | 17x17x3mm cooling fan, i know its small. Short life span, so thats why 2 pcs.
slicon wires awg17 | 20.00 | 5.49 | Aliexpress | for motors and power, black and red
cheap hubs from aliexpress. | 25.00 | 6.87 | Aliexpress | I am worried that my DIY BJ ones may be not aligned very well
awg32 wires | 20.00 | 5.49 | Aliexpress | for sensors
Electronic parts (for example: stm32H5, CAN transreciver, IMU) | 1000.00 | 274.65 | DigiKey (cheapest here) | like MCU, connector, buck conv, MOSFETs… Letme know if anyone need exact BOM here
Fast laser distance sensors 5pcs | 500.00 | 137.32 | Botland (pretty cheap shop in PL) | Not-so-cheap, but cracy fast and crazy accurate. I recommend +1 pcs beacuse you can burn them easly
My friends time, spent painting ceil to be pretty | 0.00 | 0.00 | friends which leave nearby c.o.o. | priceless

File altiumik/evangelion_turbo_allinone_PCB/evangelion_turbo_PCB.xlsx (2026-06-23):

Comment | Description | Designator | Footprint | LibRef | Quantity
1uF- | MLCC Capacitor | C1, C2, C5, C6, C7, C13, C14, C30, C36, C38, C40, C42, C44, C45, C46, C47, C48, C52, C54, C55, C58, C59, C62, C64, C65, C68 | C 0402 | Capacitor | 26
100nF- | MLCC Capacitor | C8, C10, C11, C12, C16, C17, C18, C19, C29, C31, C35A, C35B, C35C, C35D, C35E, C35F, C35G, C35H, C37, C39, C41, C43, C53, C56, C57, C60, C61, C63, C66, C67, C69 | C 0402 | Capacitor | 31
10pF - | MLCC Capacitor | C21, C22 | C 0402 | Capacitor | 2
TL8B0336M020C (2* 10uF 50v low esr) | Capacitor Polarised | C23 | CAPPC3528X100N | TL8B0336M020C | 1
22uF (10uF)- | MLCC Capacitor | C24 | C 0805 | Capacitor | 1
1000pF / 1nF- | MLCC Capacitor | C25A, C25B, C25C, C25D, C70A, C70B, C70C, C70D | C 0402 | Capacitor | 8
10uF- | MLCC Capacitor | C26 | C 0805 | Capacitor | 1
22uF 16V- | MLCC Capacitor | C27, C32 | C 0805 | Capacitor | 2
10uF 16v- | MLCC Capacitor | C28, C34 | C 0805 | Capacitor | 2
2.2uF (1uF + 1uF)- | MLCC Capacitor | C49 | C 0603 | Capacitor | 1
4.7uF- | MLCC Capacitor | C50 | C 0603 | Capacitor | 1
! | Zener Diode sod523 | D1, D2 | SOD523 | BZX585 | 2
BAS5202VH6327XTSA1 ! | Schottky Diode | D3 | SODFL1608X59N | BAS5202VH6327XTSA1 | 1
BAV199W-7 | Diode | D4 | SOT65P210X110-3N | BAV199W-7 | 1
1N4148WT-7 | Diode | D5, D9, D10, D11 | 1N4148WT7 | 1N4148WT-7 | 4
LED BLUE- |  | D6, D_5V | LED 0603 BLUE | LED BLUE | 2
LED RED- |  | D7, D_VCC | LED 0603 RED | LED RED | 2
LED GREEN- |  | D8, D_3.3V | LED 0603 GREEN | LED GREEN | 2
DF53-4S-0.6H | Connector | FAN1, LINE1, LINE2, LINE3, LINE4, LUNA1, LUNA2, LUNA3, LUNA4, MAIN_DR1, MAIN_DR2, PROG_DR2, PROG_DR3 | DF534S06H | DF53-4S-0.6H | 13
banana_plug | banana plug for high current scenarios | GND, VCC | Banana plug 2mm-smol | banana_plug | 2
STM32H562RIV6 | Integrated Circuit | IC1 | QFN40P800X800X100-69N-D | STM32H562RIV6 | 1
AZ1117CR2-3.3TRG1 | Integrated Circuit | IC2 | AZ1117CR33TRG1 | AZ1117CR2-3.3TRG1 | 1
AP63203WU-7- | Integrated Circuit | IC3 | AP63203WU7 | AP63203WU-7 | 1
AT24C02D-MAHM-E | Integrated Circuit | IC4 | SON50P300X200X60-9N | AT24C02D-MAHM-E | 1
LSM6DSV320XTR | Integrated Circuit | IC5 | LSM6DSV16BXTR | LSM6DSV320XTR | 1
TCAN1042VDRBTQ1 | Integrated Circuit | IC6 | SON65P300X300X100-9N-D | TCAN1042VDRBTQ1 | 1
TSOP57438TT1 | Integrated Circuit | IC7 | TSOP57438TT1 | TSOP57438TT1 | 1
NOPE- | Resistor | J1, J2 | ERJ1GNF1000C | ERJ1GNJ103C | 2
MLE-102-01-G-DV | Connector | J3, J4 | MLE10201GDV - ir receiver | MLE-102-01-G-DV | 2
22uH- | General pourpouse inductor | L1 | L 0805 | Inductor | 1
Buzzer |  | M? | HCT5020A | HCT5020A | 1
oled flex 0.96 |  | OLED1 | oled flex 0.96 | oled flex 0.96 | 1
4 PIN |  | PROG, PROG_DR1, PROG_DR_1 | BM04B-SRSS-TB | 4 PIN | 3
P mos power- |  | Q1, Q2 | dfn33 | P mos power | 2
Model | General Pourpouse Mosfet | Q3 | SOT323 | N Mosfet | 1
Model | General Pourpouse Mosfet | Q4 | SOT23-3 | N Mosfet | 1
10k- | General pourpouse resistor | R1, R2, R4, R7, R9, R12, R17, R19, R21, R23, R24, R25, R26, R27, R32 | R 0402 | Resistor | 15
47K (56k)- | General pourpouse resistor | R3 | R 0402 | Resistor | 1
1K- | General pourpouse resistor | R5A, R5B, R5C, R5D, R5E, R5F, R5G, R5H, R22, R34 | R 0402 | Resistor | 10
470R (330R)- | General pourpouse resistor | R6 | R 0402 | Resistor | 1
4.7K- | General pourpouse resistor | R10, R11, R15, R16, R28, R30, R31 | R 0402 | Resistor | 7
330R- | General pourpouse resistor | R18, R35, R36, R37 | R 0402 | Resistor | 4
91k- | General pourpouse resistor | R20 | R 0402 | Resistor | 1
390K- | General pourpouse resistor | R29 | R 0402 | Resistor | 1
2.1K (2K)- | General pourpouse resistor | R33 | R 0402 | Resistor | 1
300R | General pourpouse resistor | R38A, R38B, R38C, R38D, R39A, R39B, R39C, R39D | R 0402 | Resistor | 8
SKRHABE010 | Switch | S1 | SKRHABE010 | SKRHABE010 | 1
EG1271A | Switch- | S2 | EG1271 | EG1271A | 1
US3200005Z | Crystal or Oscillator | Y1 | US3200005Z | US3200005Z | 1

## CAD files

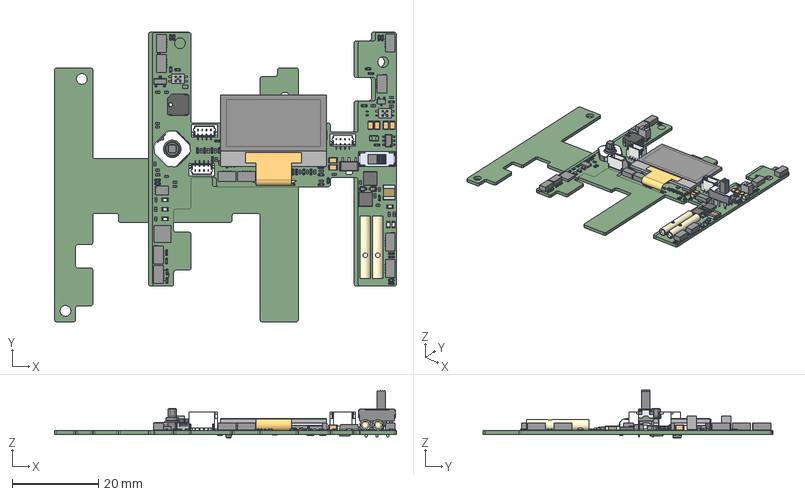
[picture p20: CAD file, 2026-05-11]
inventor-project/PCBMain.step
79.4 x 67.3 x 11.0 mm
Rezystor_0402 x 49
Resistor_0402 x 67
SOT23-3 x 4
SMD-5025-0340-12Š
MLE-102-01-DV_socket x 2
C-99-01-02 x 2
Pins x 14
oledzik
Pin_PCB-Female x 2
PinsArrayL x 2
FilletPinR x 2
\X2\FFFDFFFD\X0\1 x 2
\X2\FFFDFFFD\X0\2 x 2
BM4B-SRSS-TB x 3
Pin1
Pin2
CeramicBody
solidBody x 2
Terminal x 2
solidTop x 2
ThermalPin x 3
PinsArrayLR x 3
PinsArrayTB
0603_Red x 14
0603_Blue x 14
0603_Green x 14
PinKIdent
PinK
PinA
SOD-523 x 2
C0603_060 x 6
C0805_125 x 18
PCB_InterfaceBoard
PCB_InterfaceBoard_3613820680 x 2

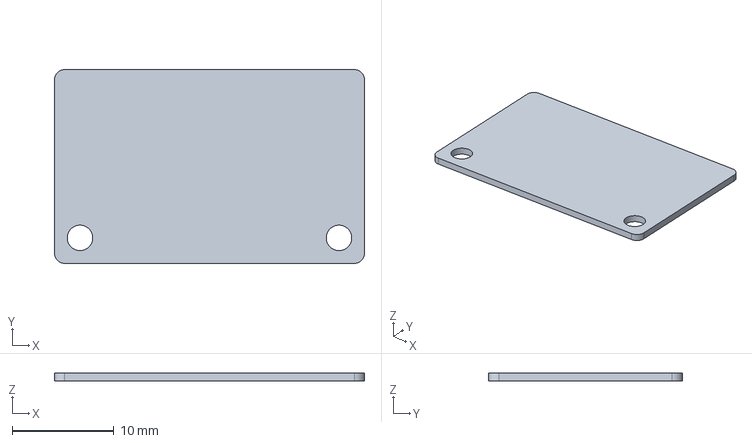
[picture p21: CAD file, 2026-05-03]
altiumik/BoardShapes/PCB_Main.stp
30.4 x 19.0 x 0.8 mm

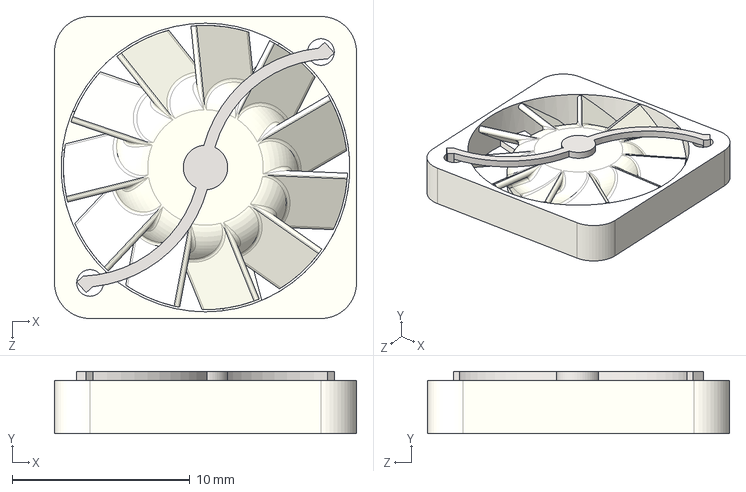
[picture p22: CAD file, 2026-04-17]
inventor-project/1703 Fan asm.STEP
17.0 x 3.50 x 17.0 mm

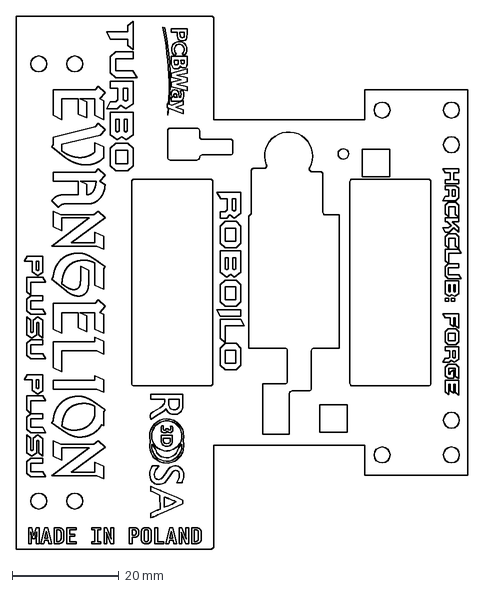
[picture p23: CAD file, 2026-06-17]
3DP/Laser cutting/stal_2mm-dach_z_grawerem-sponsory.dxf
84.7 x 100.0 mm

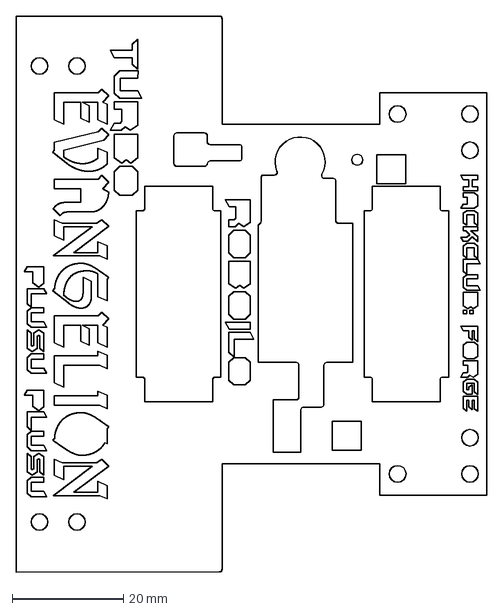
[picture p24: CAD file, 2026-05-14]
3DP/Laser marking/Dach.dxf
84.7 x 100.0 mm

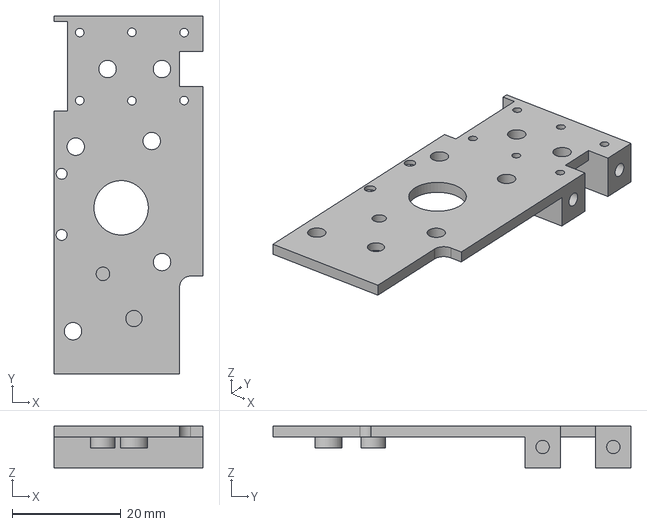
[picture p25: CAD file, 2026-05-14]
3DP/SLM/LeftGearboxCoverr.stp
27.4 x 65.8 x 7.70 mm

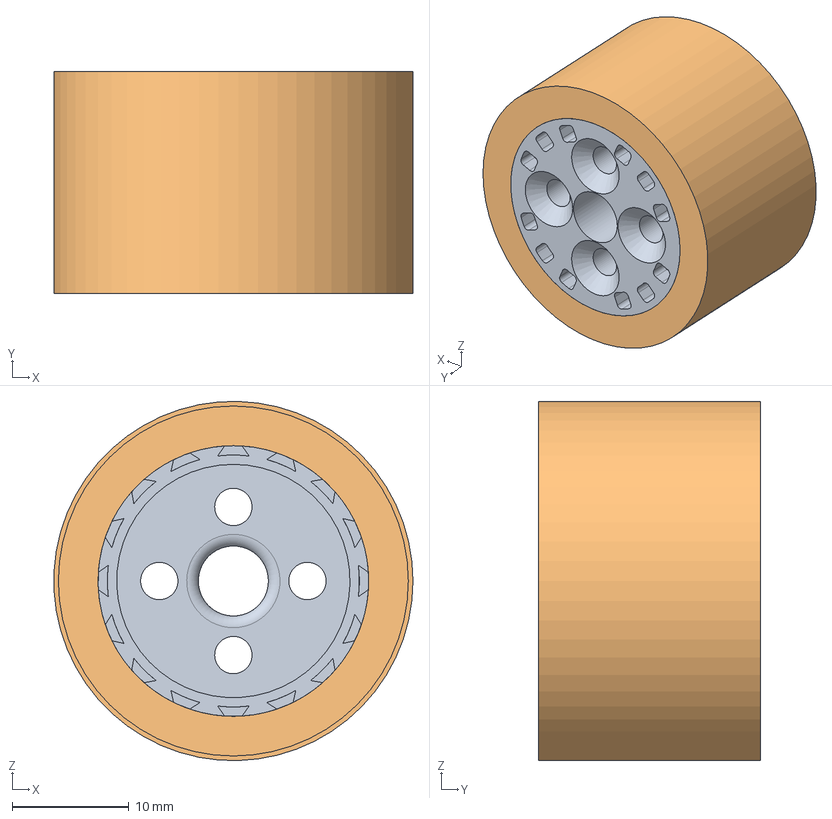
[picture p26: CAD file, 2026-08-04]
3DP/SLS/Felga2XForma.stp
30.8 x 19.0 x 30.8 mm
Felga
FelgaForma

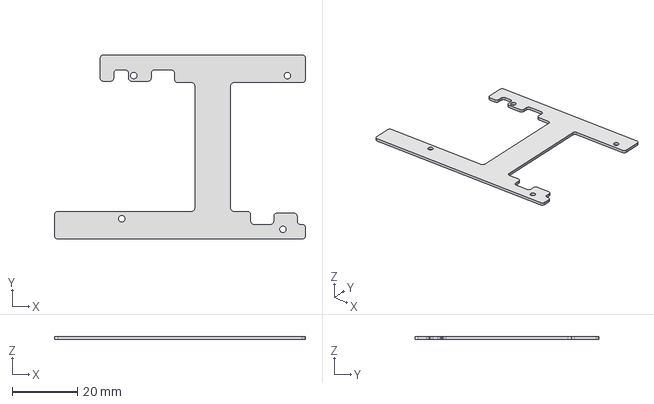
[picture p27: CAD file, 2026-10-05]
altiumik/BoardShapes/PCB_interface_allinone.stp
77.0 x 56.5 x 1.00 mm

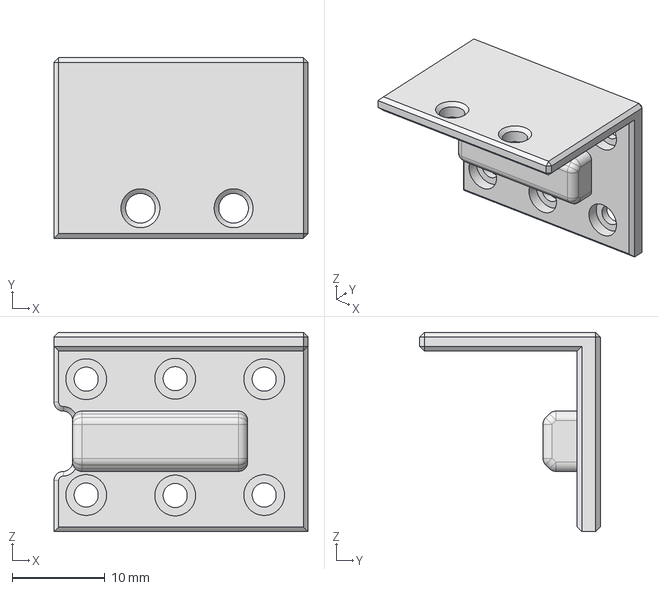
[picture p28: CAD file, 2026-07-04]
inventor-project/BackLunaRecoveryHold.stp
27.4 x 19.5 x 21.5 mm

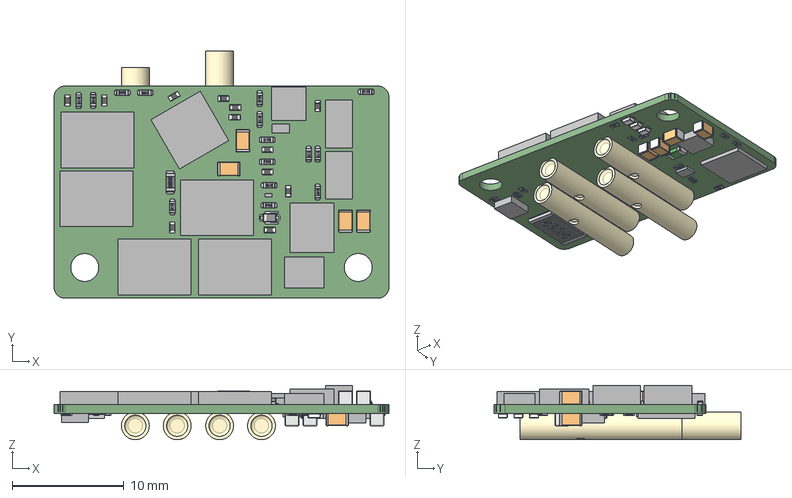
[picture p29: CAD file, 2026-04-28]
inventor-project/MotorDriver/PCB_Motors.step
30.0 x 22.2 x 4.87 mm
Extruded x 17
C0805_125 x 24
Rezystor_0402 x 20
Resistor_0402 x 19
Pin_PCB-Female x 4
Resistor_0603
Resistor_2512
Pin1
Pin2
CeramicBody
SOD-523
0603_Green x 7
0603_Blue x 7
0603_Red x 7
PCB_Main

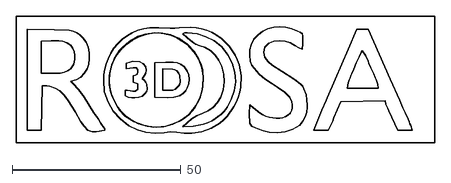
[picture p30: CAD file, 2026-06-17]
Ultra important resources/ROSA.dxf
123.8 x 37.6

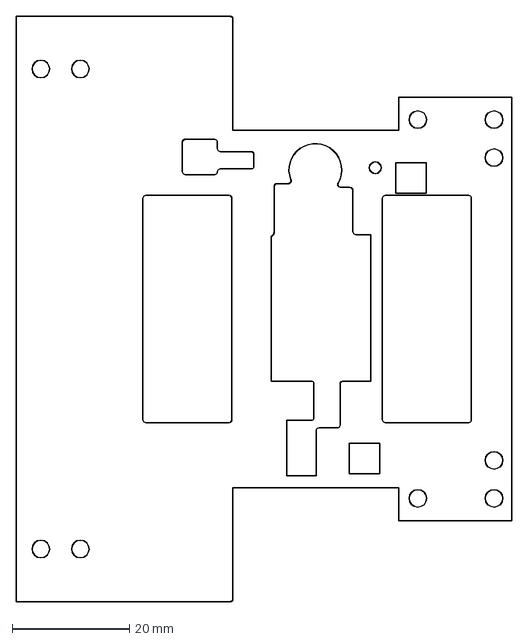
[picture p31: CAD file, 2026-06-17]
3DP/Laser cutting/stal_2mm-dach_bez_graweru-sponsory.dxf
84.7 x 100.0 mm

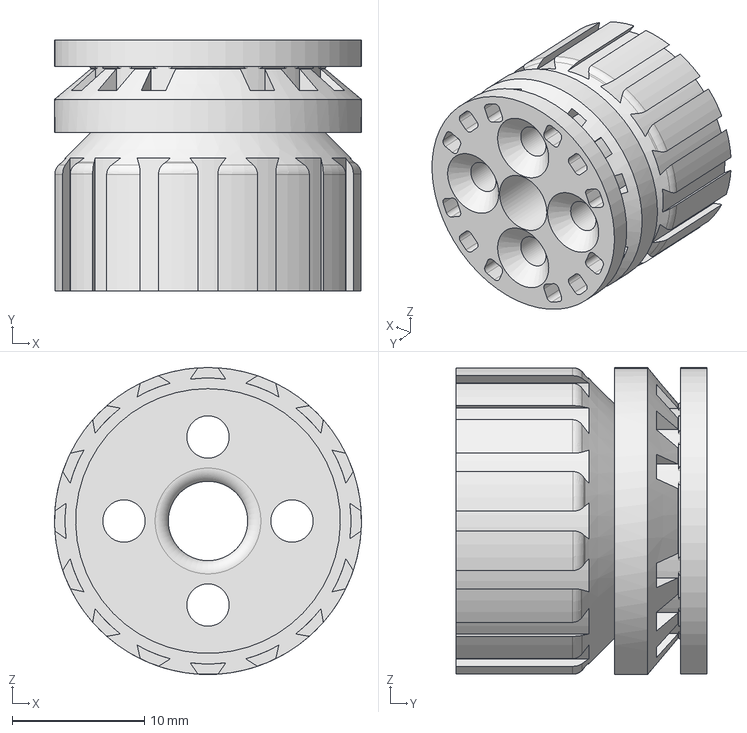
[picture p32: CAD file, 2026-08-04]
3DP/SLS/felga2.stp
23.2 x 19.0 x 23.2 mm

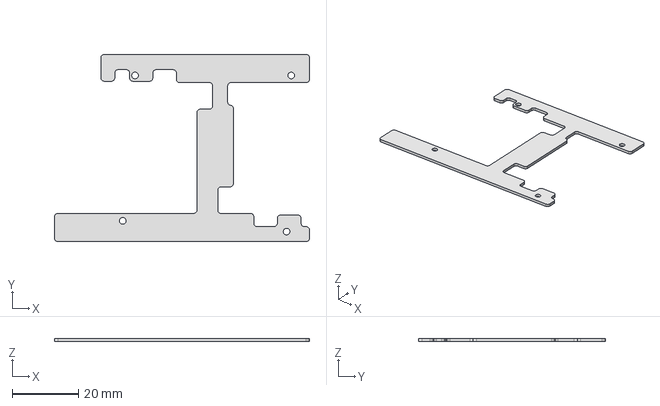
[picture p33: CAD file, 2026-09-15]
altiumik/BoardShapes/PCB_interface_v2.stp
77.0 x 56.5 x 1.00 mm

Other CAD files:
inventor-project/main.dwg
3DP/SLM/RightGearboxCover.stp
Ultra important resources/PcbWay.dxf
3DP/Laser cutting/1mm_aluminium_2szt-Front.dxf
3DP/Laser cutting/1mm_aluminium_2szt-Tyl.dxf
3DP/Laser cutting/1mm_stal_2szt-Tyl.dxf
3DP/Laser cutting/2mm_stal_1szt-Dach_bez_graweru-stary.dxf
3DP/Laser cutting/2mm_stal_1szt-Dach_z_grawerem-stary.dxf
3DP/Laser marking/Dach.dwg
3DP/SLM/DiyHub.stp
3DP/SLM/FonrtMount.stp
3DP/SLM/LeftGearbox.stp
3DP/SLM/RightGearbox.stp
3DP/SLM/plug-fix.stp
3DP/SLS/FLAT_PLOW_x2.stp
3DP/SLS/Felga.stp
3DP/SLS/FonrtMount.stp
3DP/SLS/GearboxBearingHolderCover.stp
3DP/SLS/GearboxBearingHolderCover_MIR.stp
3DP/SLS/LeftGearbox.stp
3DP/SLS/PCBs_Holder.stp
3DP/SLS/RightGearbox.stp
3DP/SLS/RightGearboxCover.stp
Ultra important resources/Chamferer.ipt
Ultra important resources/Hackclub.dxf
Ultra important resources/Katze.dxf
altiumik/BoardShapes/LeftGearboxCoverr.stp
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

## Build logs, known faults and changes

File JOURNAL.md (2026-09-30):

---
title: "Evangelion Turbo"
author: "Szymon Filipkowski"
description: "Evangelion Turbo is an SUMO robot of footprint 10x10cm and weighing less than 1kg. It is direct successor to my last robot, Evangelion. Evangelion have 4 distance sensors, 4 line sensors, IMU, oled, UI and maybe even enkoders (idk if i will fit them tho)"
created_at: "2026-03-16"
---

# March 07: Designed the PCB layout
First idea. I decided that i want to go with Pololu 37D chunky motors - beacuse they are more powerfull and more chunkier than motors i have in my previous robot, Evangelion.
I revied every option i had on had. Pololu 25D, some chinese motors, like RS395. Pololus seems the best for this. We well see what CAD will tell thus.
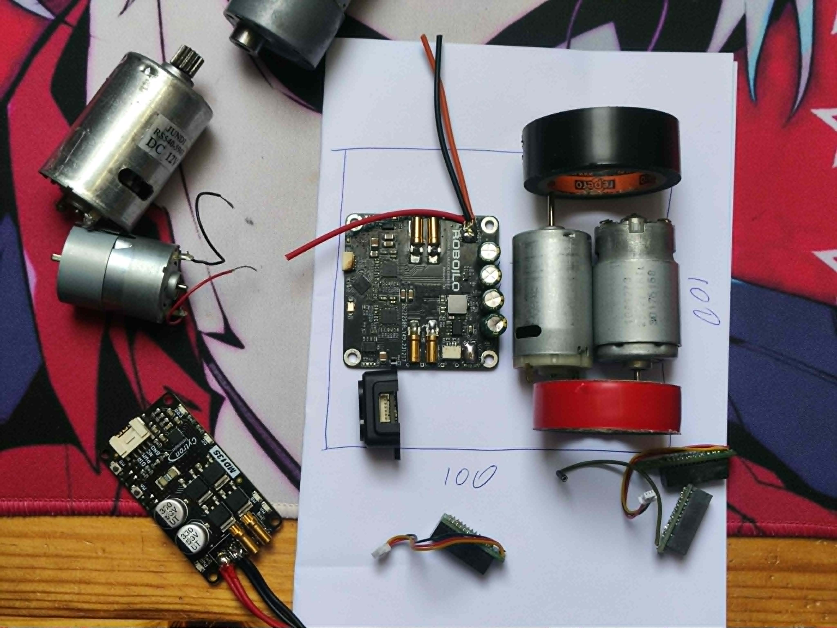
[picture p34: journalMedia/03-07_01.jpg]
Layout

**Total time spent: 2 hours**

# March 09: CADding!
So today i spent some time playing with cad, sensors ETC. CAD told me "NAH" pololu 37D would be too big :(
I really wanted to FORCE THEM TO FIT... So i spent a looooot of time trying anything. After all i decided that they are too heavy (bcoz i want this robot to be able to start in 500G weight too).
Sooooooo i decided to put same motors as in my previous robot, evangelion! And to make them better, take out one gear from gearboxes, making this robot a lil bit faste (19:1 changed to 7.5:1).
Gears from pololu 37D already worked for me so for this robot i plan to use it too, but orded cheaper, from aliexpress, instead of the original ones. I added them to cad and made all of the needed constraints.
I measured and added LIPO batteries to test if i even can fit any of them (2s and 3s, 450 and 550mAh).
Aaaalso i made double shear bearings, like in the VORONs. I like 3d printer and vorons :)
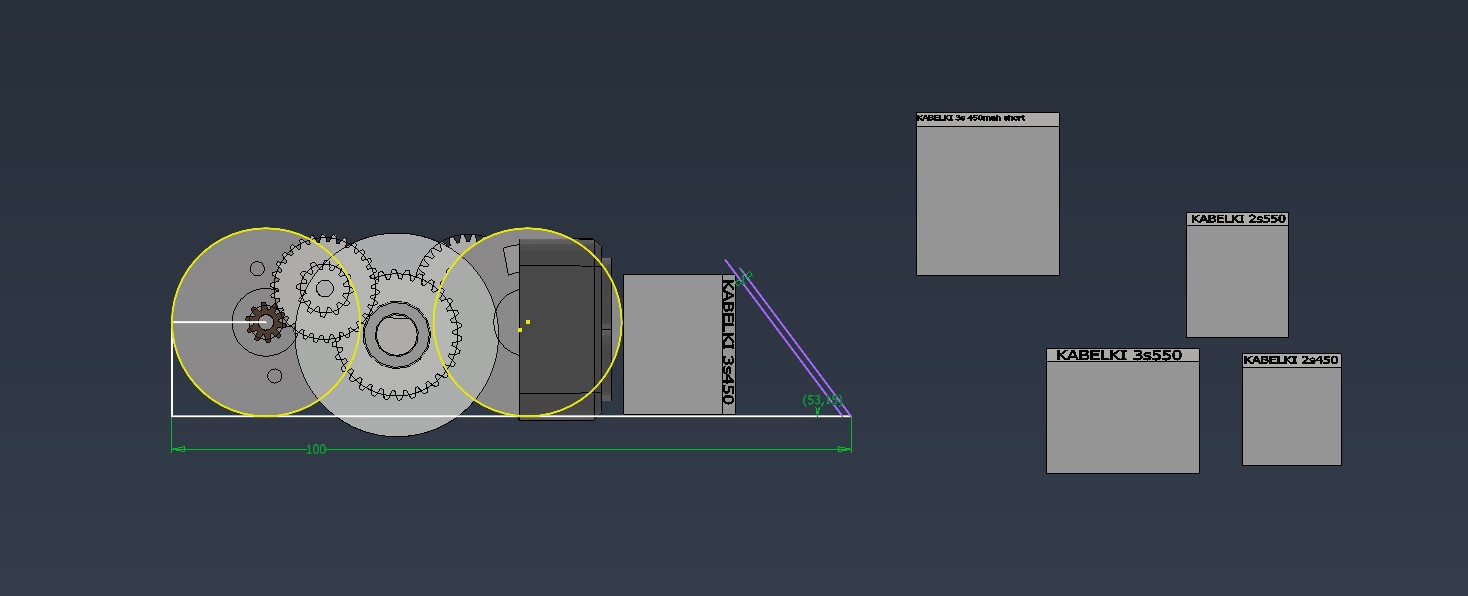
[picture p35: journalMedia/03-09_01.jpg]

**Total time spent: 8 hours**

# March 10: Who needs school when you can sit in the CAD, talk with your friends and do cool stuff?
Parents made me go to school today ;-; soo sad.
But anyway. WHO NEEDS 2 SENSORS WHEN YOU CAN HAVE 8 OF THEM! I managed to fit 8 sensors in 10x10cm sumo robot. 2 laser distances at the front. 2 IR distances pointing to the sides. 4 line sensors in each corner.

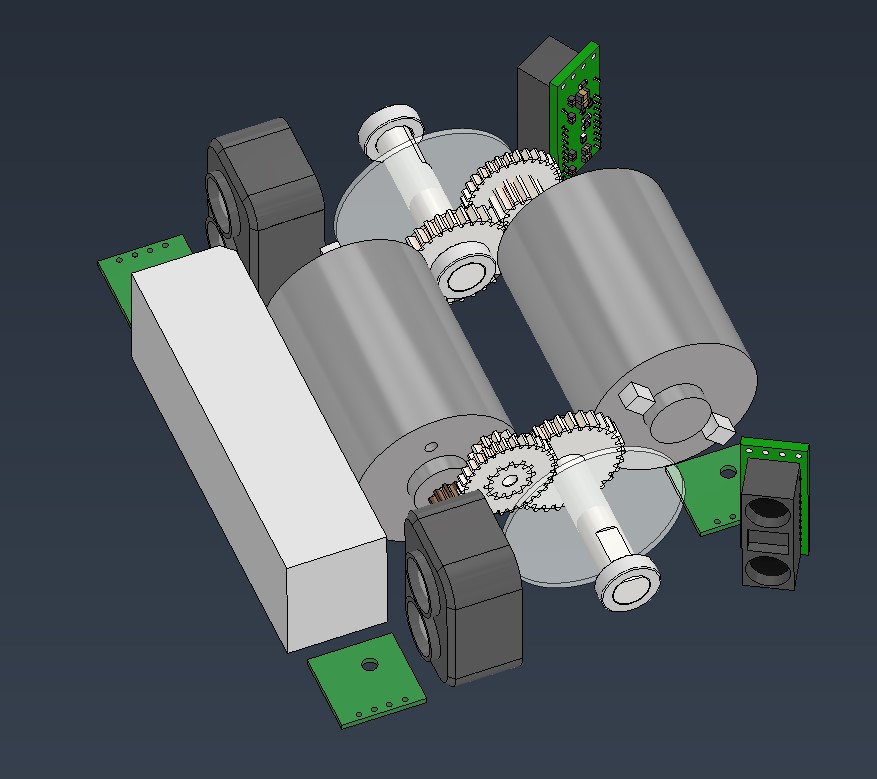
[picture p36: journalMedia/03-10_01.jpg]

**Total time spent: 4 hours**

# March 11: WHO NEEDS 2 SENSORS WHEN YOU CAN HAVE 10 OF THEM
YESSIR! There are 10 of them now! I managed to add extra two IR distance sensors!
HELLNAH, yesterday i forgor that wheels _do_ exists. I had to made back sensor tilt a little bit. But they are two more of them now :) Overall it was an good evening.
TBH I dont know why it takes so much time to fit everything into so big footprint (wait... this is only 10cm so it is small XD)
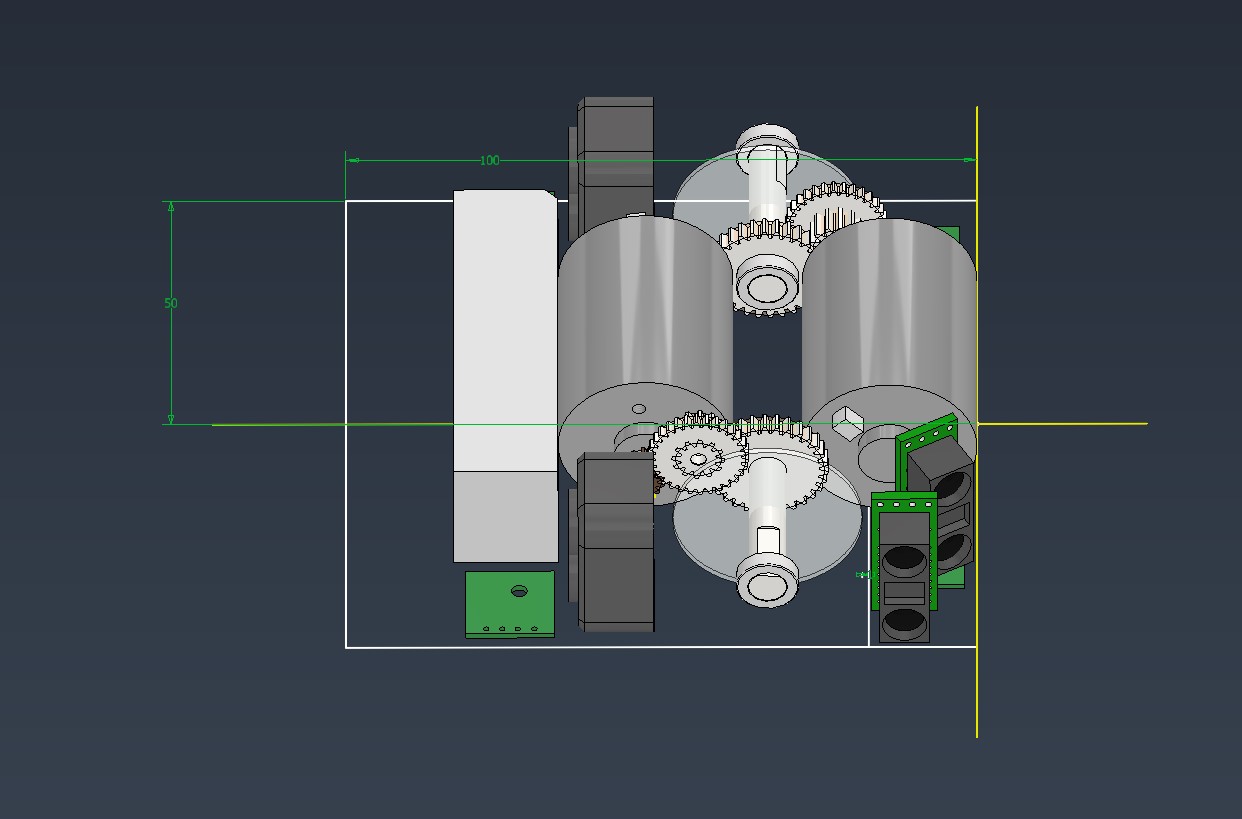
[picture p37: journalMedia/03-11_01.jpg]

**Total time spent: 3 hours**

# March 21: Competition time!
I mounted IR sensors i planned to use in this robot, in Evangelion (my previous robot which is working). I spent a few hours trying to force SHARPs (these IR sensors) to work! It turns out that these types of sensors are literally _shit_. They are painfully slow and very innacurate.
Yup. beacouse of them i have lost ;-;
Feels bad - thus not so bad, beacuse i tested sensors now, not on the RoboRave, abroad!
**Total time spent: 2 hours**

# March 23: GUYS VERY GOOD INFO!
I talked with my teachers. They let me attend only the most important lessons (like math, polish, english and physics)! No stupid history for now! I can work more! Lets goooooooooooooooooooo. :DDD

# March 25: Safety first!
After some research and rethinking my life choices i decided to bury cool idea od 10 sensors and steep front. I had to move everything to the front, to leave more space for laser sensors, to fit. After more research, big problem came up to me. EMI will kill all of my capabilities. After searching i found some motor shielding - about .7mm thick. I think it will be enough. If not - then im cooked guys.

Moving everything in cad .7mm BROKE EVERY CONSTRAIN IMAGINABLE...
remember guys. always constrain your parts to origin planes, not other parts.

So i had to spend more time redoing everything :|

After dinner i added interface board with oled.
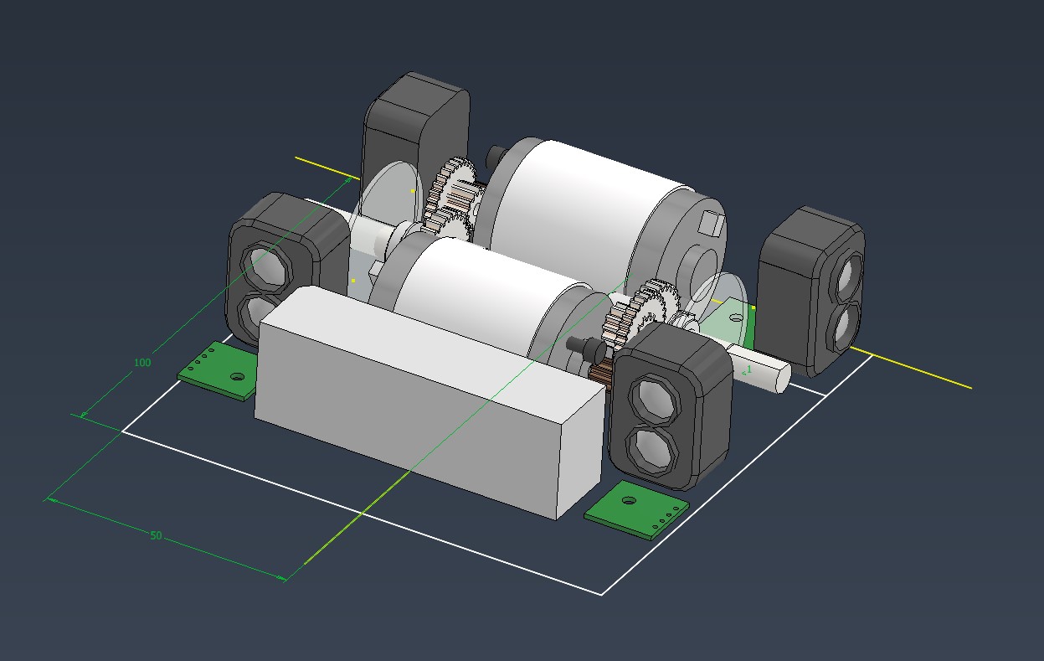
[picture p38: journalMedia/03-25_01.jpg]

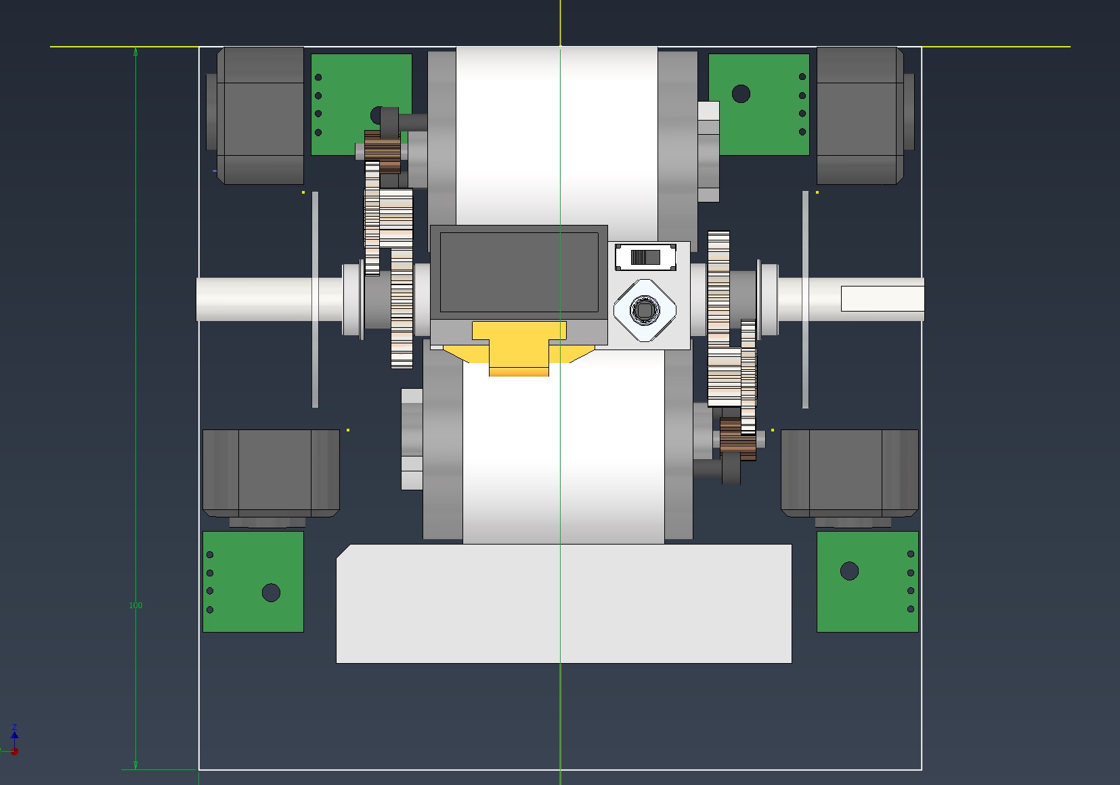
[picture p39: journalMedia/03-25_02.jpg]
CAD2

**Total time spent: 7 hours**

# March 27: Mom, look! My MCU barely fits there!
So today. Today is the big day. No procrastination and rotating model in CAD. Pure lock-in in PCB design.
Guys. If you dont use Library Loader - start using it. I discovered it via random problem in reddit. IT IS SO HELPFUL. Like you can add any part without losing time on rewriting it.

For the work, today i have made MCU with all the ports, IOC in stm32cubeide, with all of the PINs configure, power supply and low pass filter for filtering anything from analog channels.

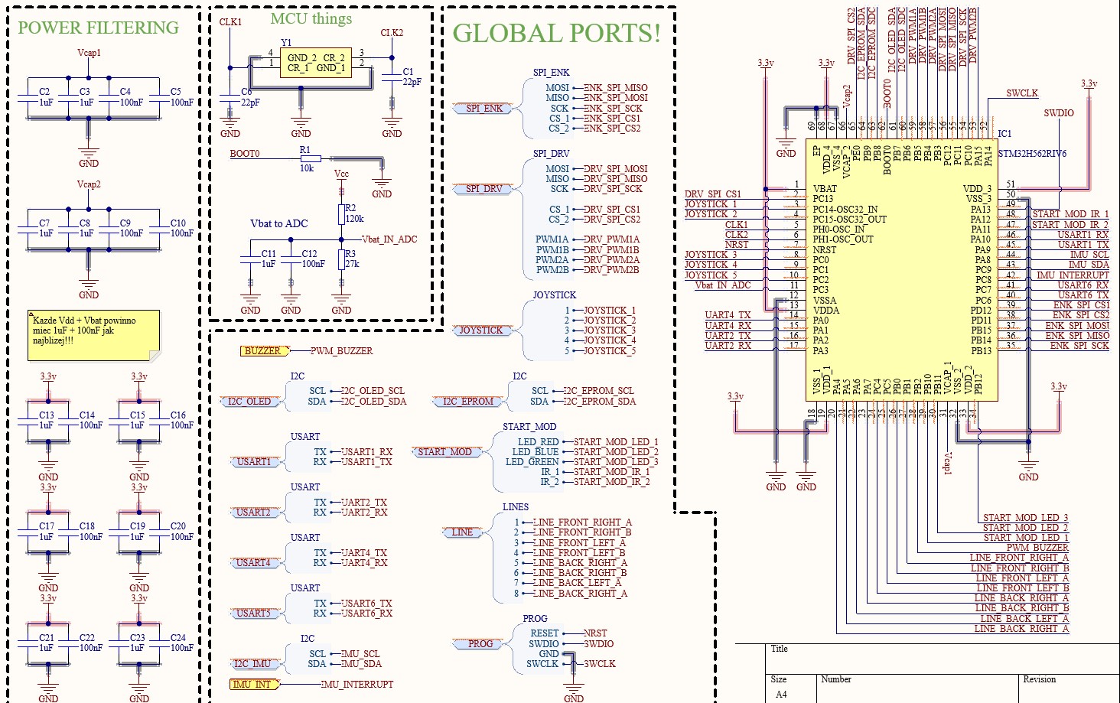
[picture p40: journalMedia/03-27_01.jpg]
Mcu schematics

**Total time spent: 4 hours**

# March 28: Any UI/Ux designer to help me? Pwetty Pwaseeeee
From the beggining of this project i wanted to use OLED without stupid additional useless piece of PCB they ship it with. My friend, managed to pull it off on his LineFollower, so i think it may _(please, work, please)_ work.
I found schematics for OLED in some random chinese website written in chinese, so wich me luck XD

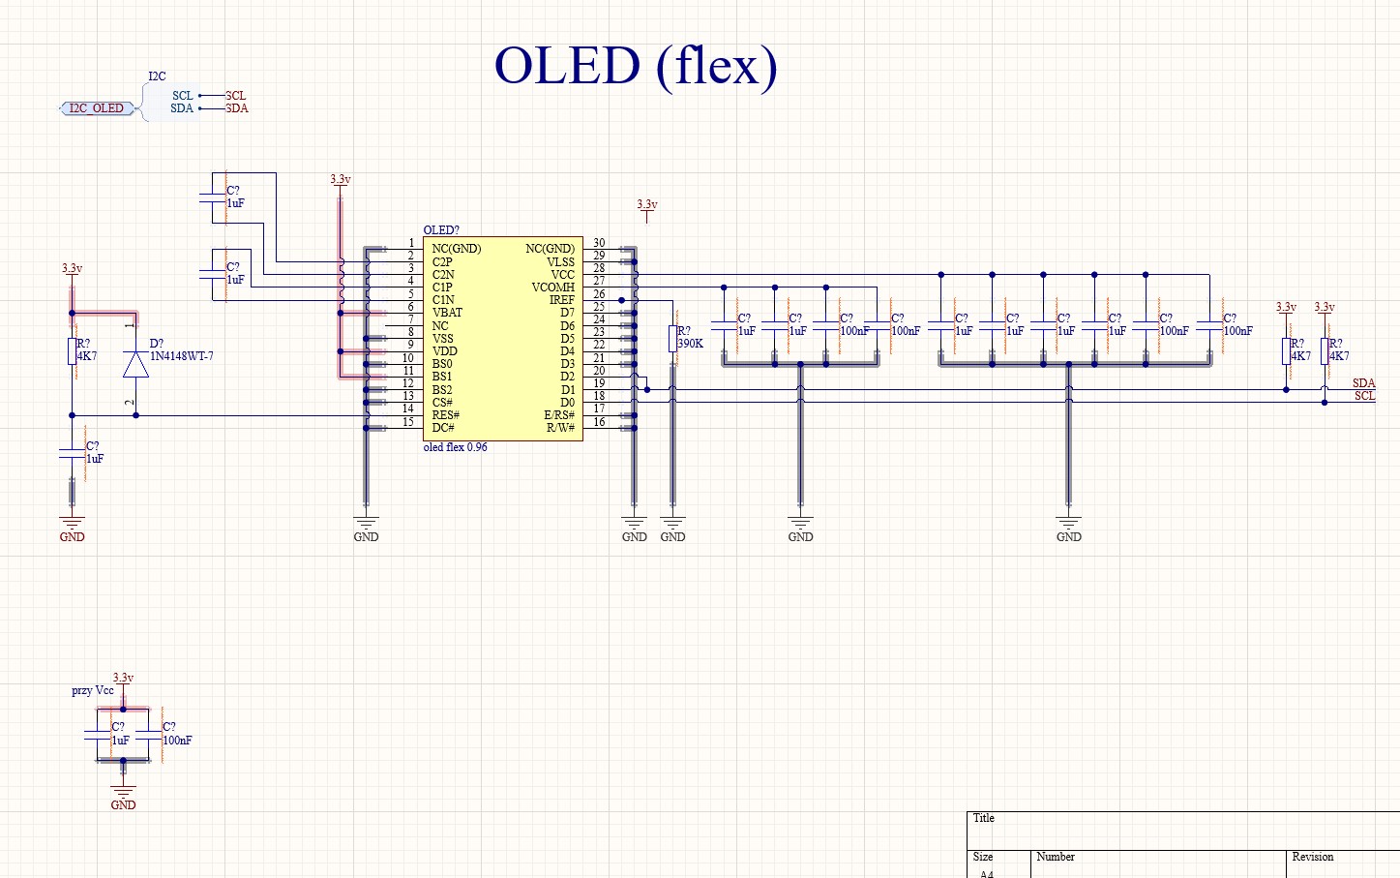
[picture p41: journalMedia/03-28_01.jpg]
OLED

**Total time spent: 3 hours**

# March 29: Interface? Not the UI tho
Today, at school, i thought "Wouldnt be cool to have one push button, to turn on and off robot? And ofc fully electrical/mechanical, no GPIO involved". Yea guys. Its alive. After tinkering in electric simulation and coutless arduino toturials i have found it.
I was bored, so i also made schematics for power supply. Buck conv from lipo 3s to 5v and ldo from 5v to 3.3v.
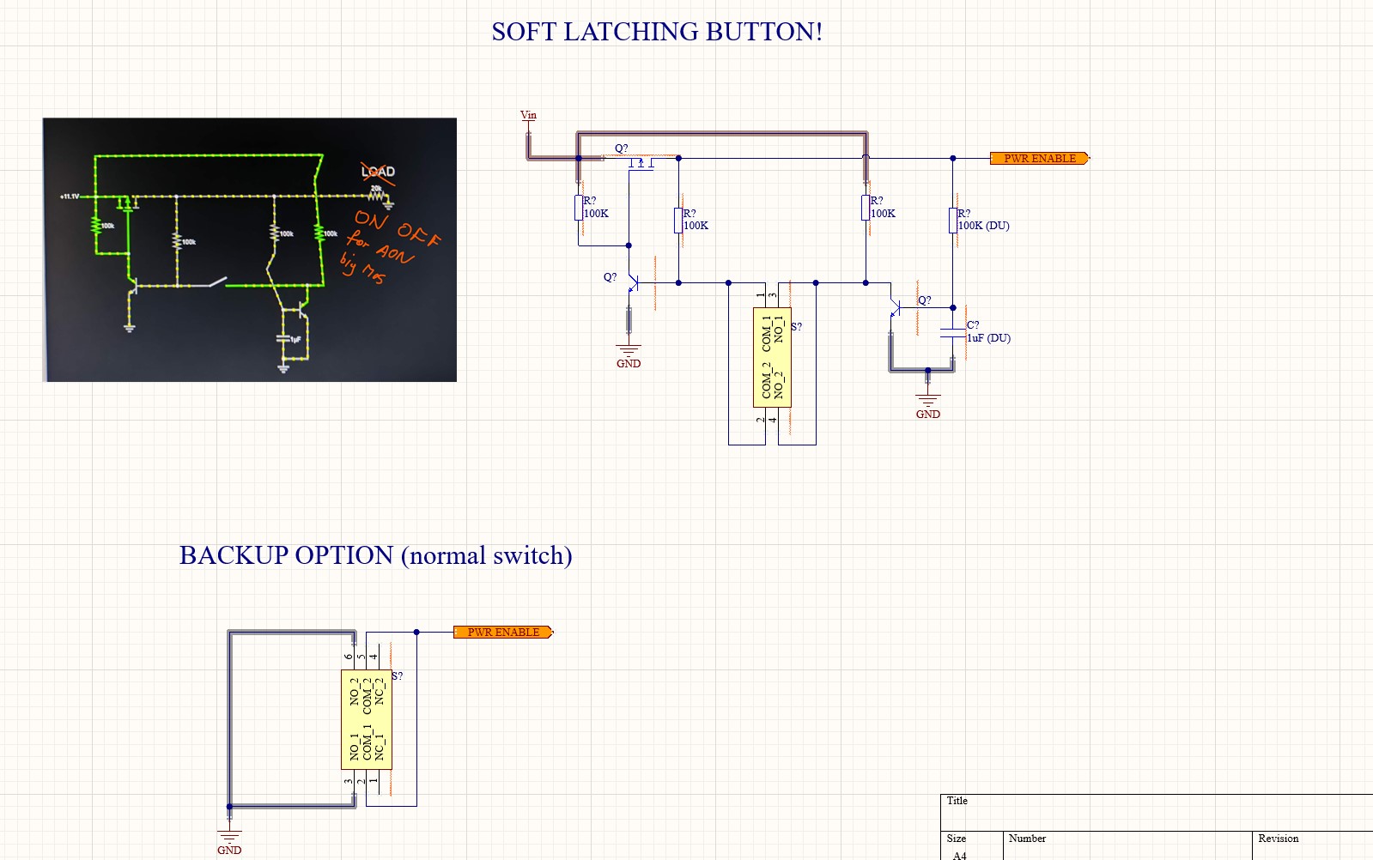
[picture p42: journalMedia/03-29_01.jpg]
Soft latching button

**Total time spent: 4 hours**

# April 1: High current? Please be enough this time
In my previous robot, Evangelion, motors were highly limited by drivers (they were limited to about 3A). Theoretically motors in spike are pulling about 5A and drivers could withstand up to 4.2A. But taking no cooling and hot chasish into consideration DRV8251 limited them to aboud 3A. So for this robot i made good research and settled on to use DRV8873 drivers. Max 10A in spike. No external mosfets, for easier routing. I want to fit two motors drivers between motors, so there is little space there.

GUYS! You can choose from hardware and software version of this driver. It accually is little driffrence. In hardware you use resistors etc to change max AMP for example, in software you do this via SPI. In both versions you need to control both drivers via PWM tho.

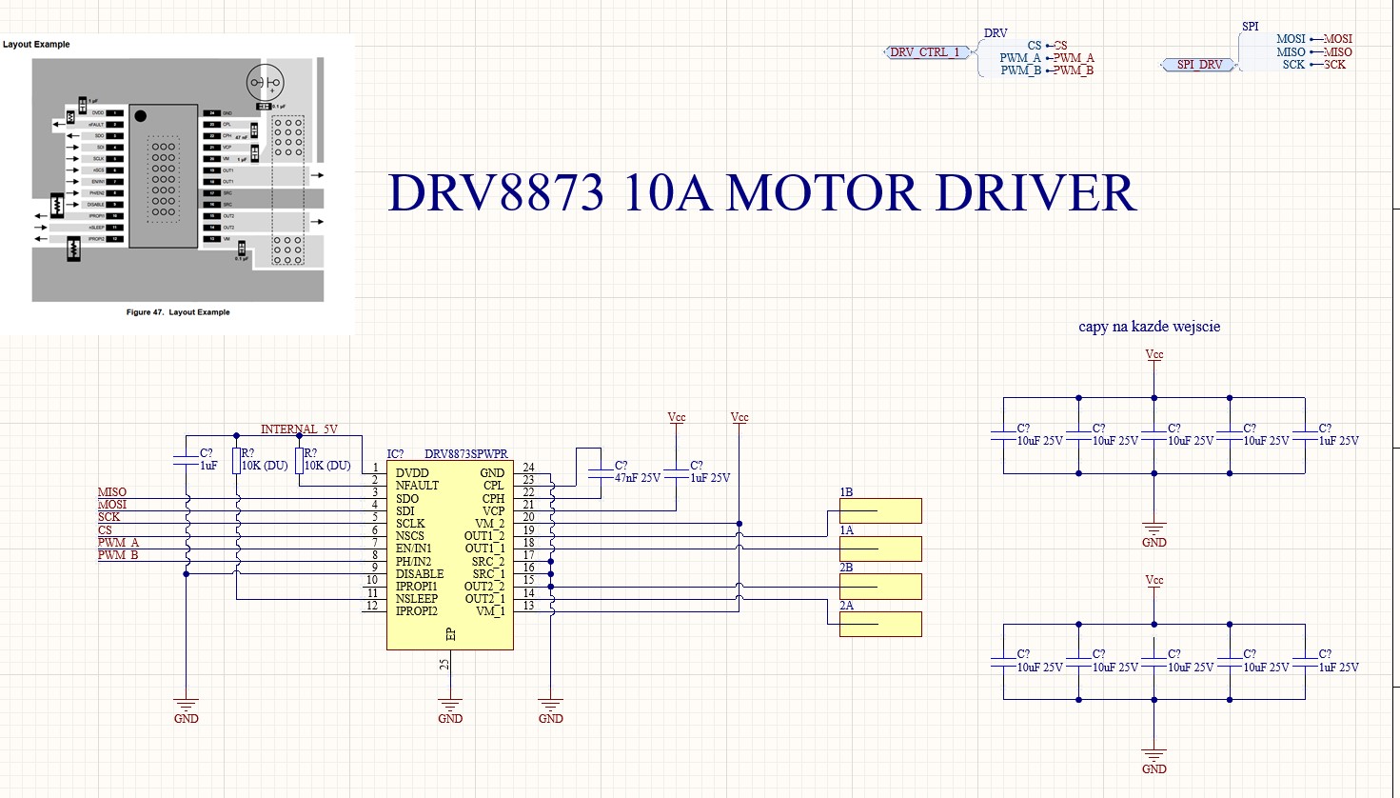
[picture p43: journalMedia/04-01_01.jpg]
drivers

**Total time spent: 3 hours**

# April 2: LOCK-IN. I may have skipped school.
Big lockin today it was. I finished doing all of the interface-controller board schematics. I didnt know how would i connect my three boards! After some research and talk with my brother, he adviced me to use BTB connector. After searching for a while i found 40pin one :D
40pin - OLED, start module, SPI to drivers, 5v, 3.3V, joystick... A lot.

Schematics for IMU and EPROM done too today!
And i even managed to fir buzzer here! (Like it is hard to do schematics for one ;-;)
Also did you guys heard about STLINK? I wanna have it on board. Research for any schematics.

Im really exhausted tho...
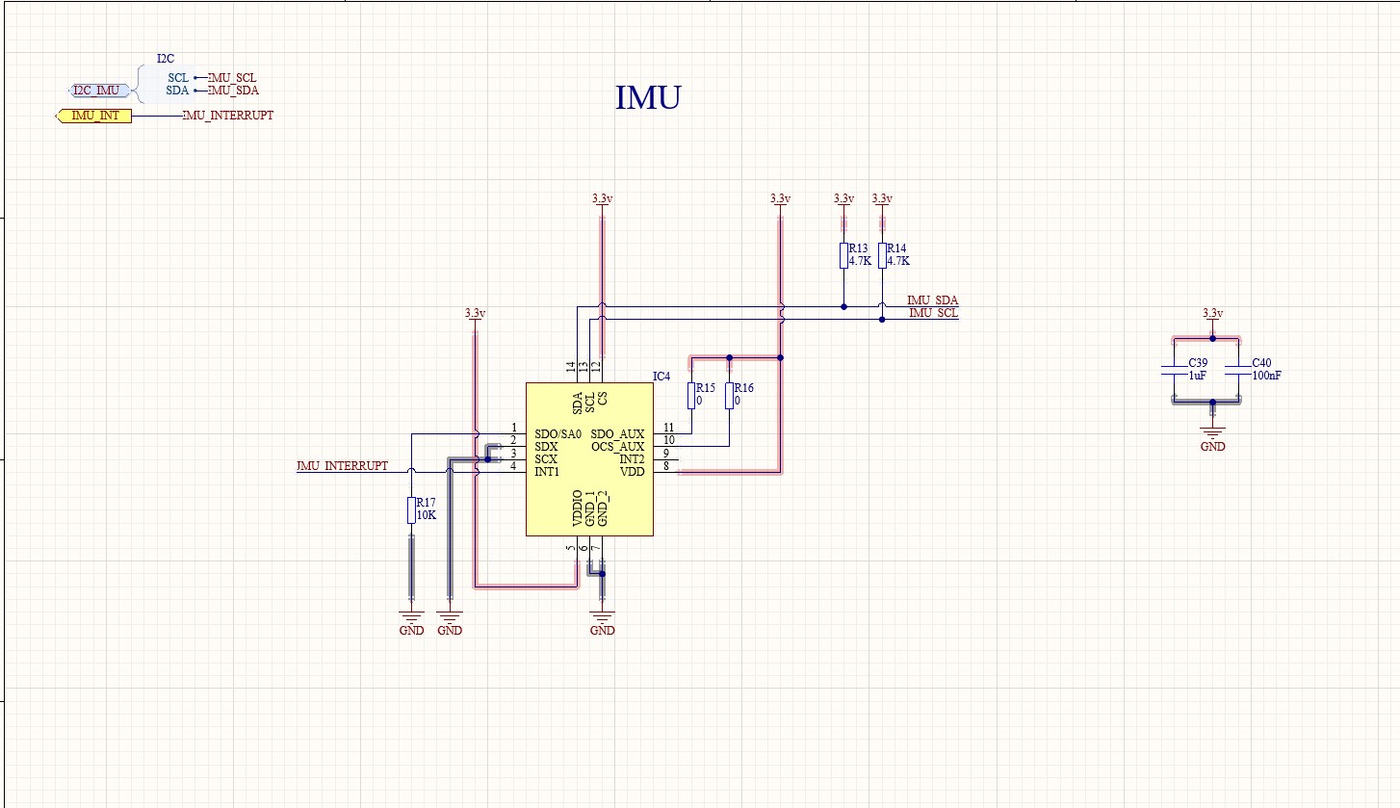
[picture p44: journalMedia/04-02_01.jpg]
Schematics1

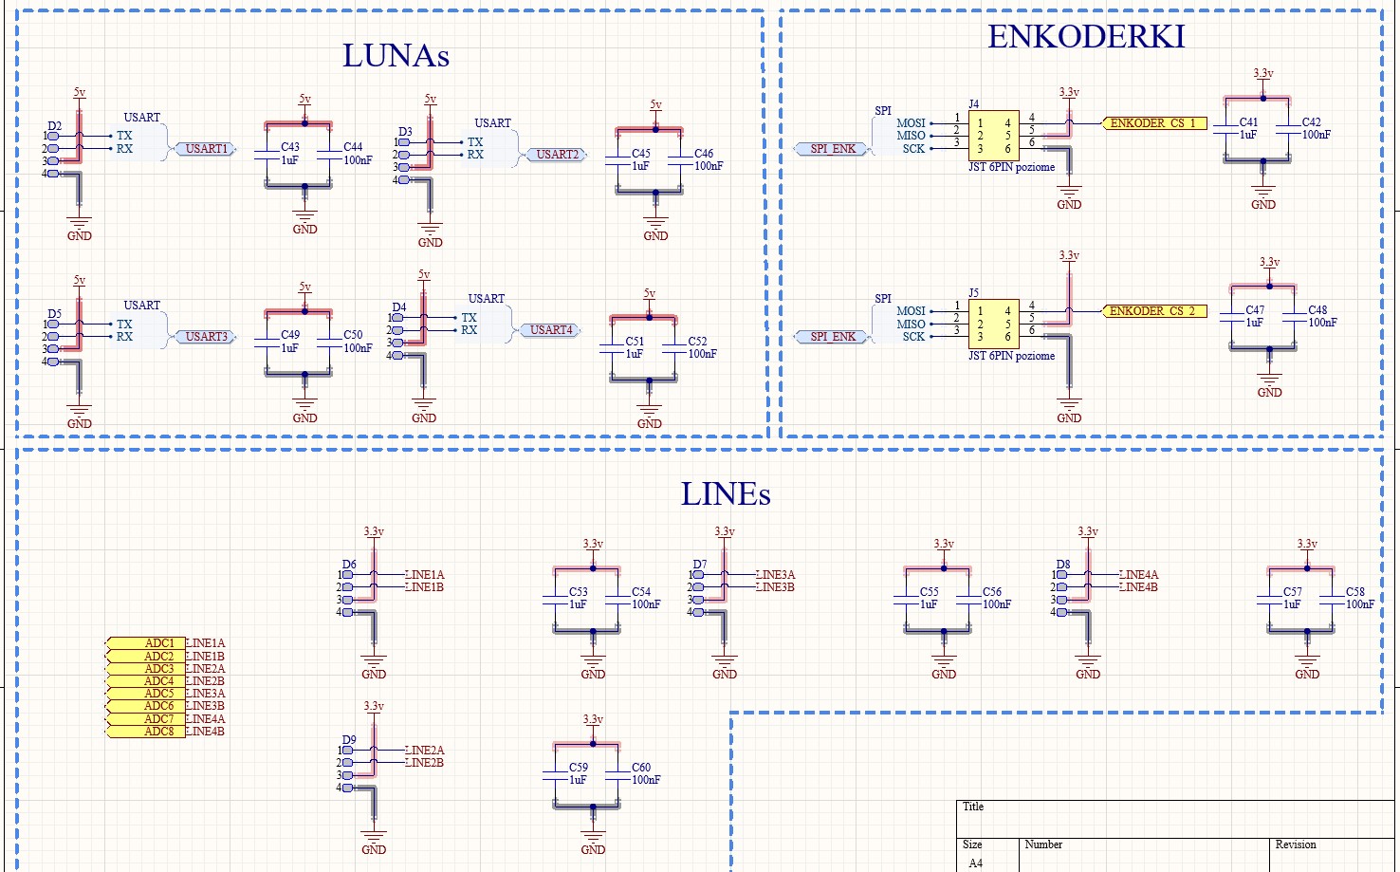
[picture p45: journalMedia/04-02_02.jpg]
Schematics2

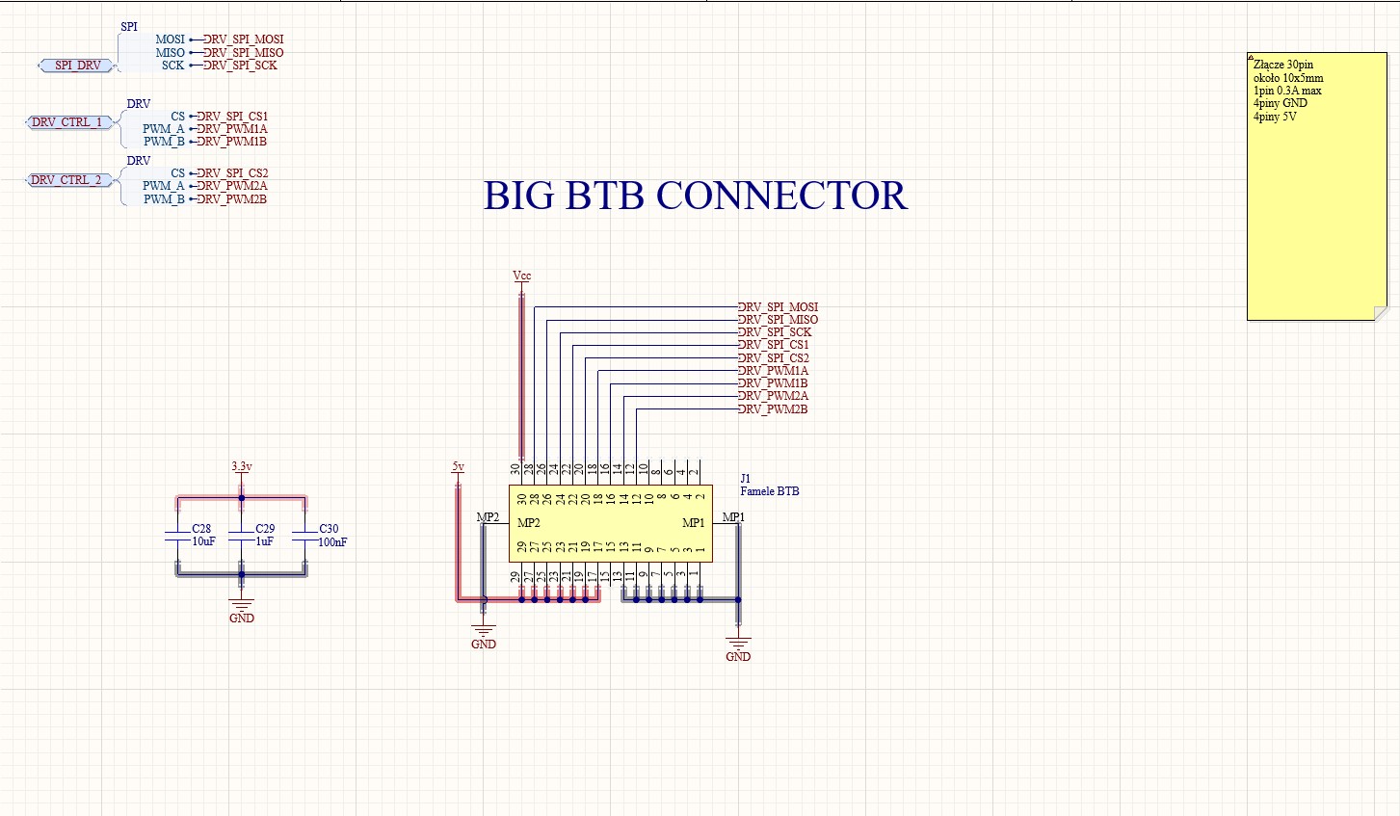
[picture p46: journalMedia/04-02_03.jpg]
Schematics3

**Total time spent: 10 hours**

# April 3: STLINKIN
I wanna stlink. On my robot.
After yesterday's research i have schematics from some random guys from github. CHATGPT told me, that i need to have some f103 MCU for this to work, and i cant use something like C0 in really small casing. At first glance i wanted to use smallest f103 I could find (something like f103 in case with BGA out pins). BUT THIS WOULDNT WORK! Chatgpt and datasheets - in the official code there are pins, that are missing in smallest f103 in bga. Soo i was forced to use some normal, big f103.

Did you know, you could damage your PCB if you dont have proper safety diodes added? I know right, this is cool physics stuff. But not cool tho - i have to add more compontents...
Yeah. You are thinking right. USB-C schematics - made by me :)

_please fit in my PCB, please fit. im worried. ik, maybe i will go with 4lyaer PCB thus?_

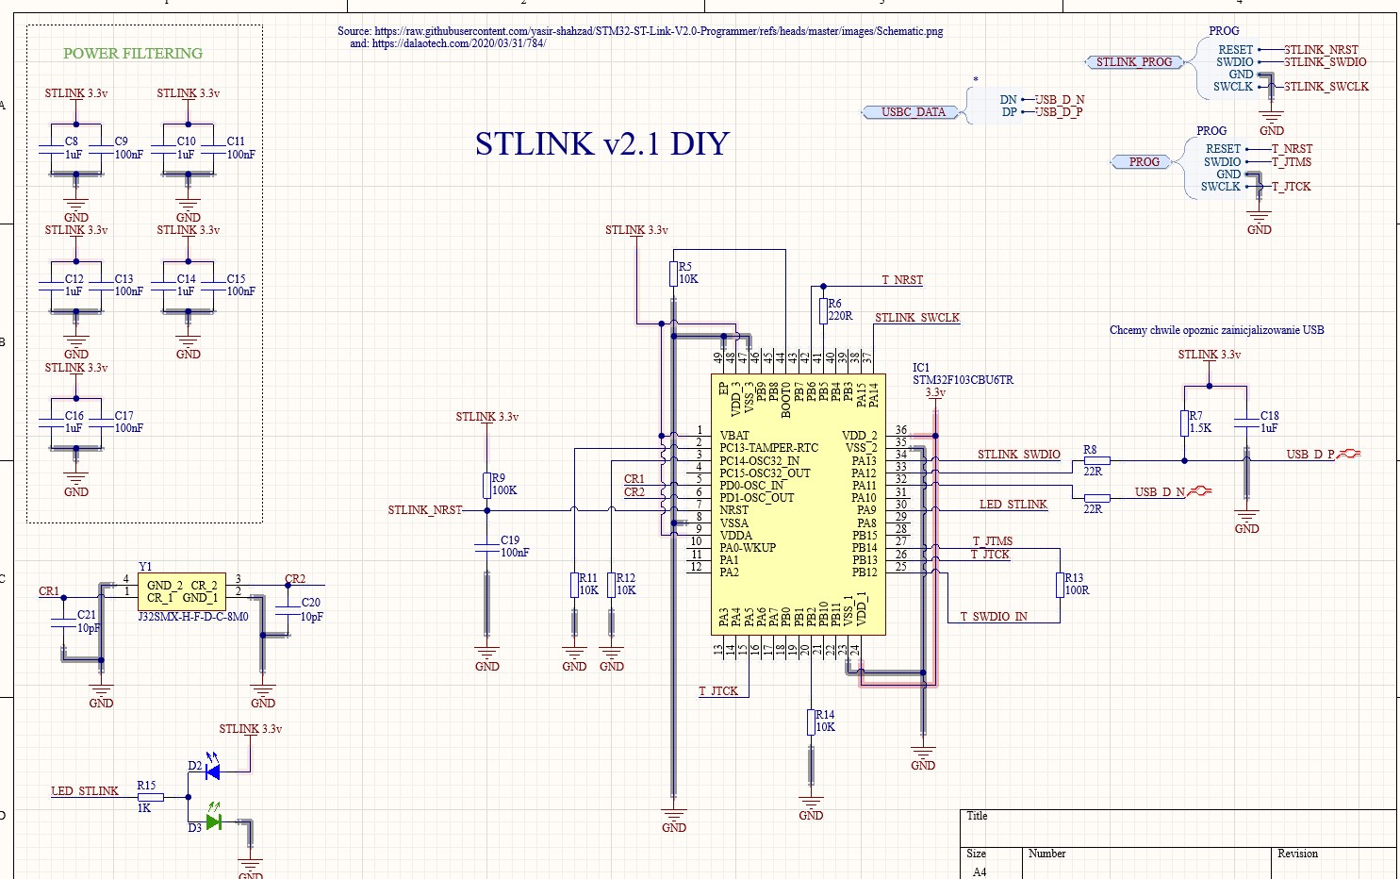
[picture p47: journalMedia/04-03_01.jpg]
link

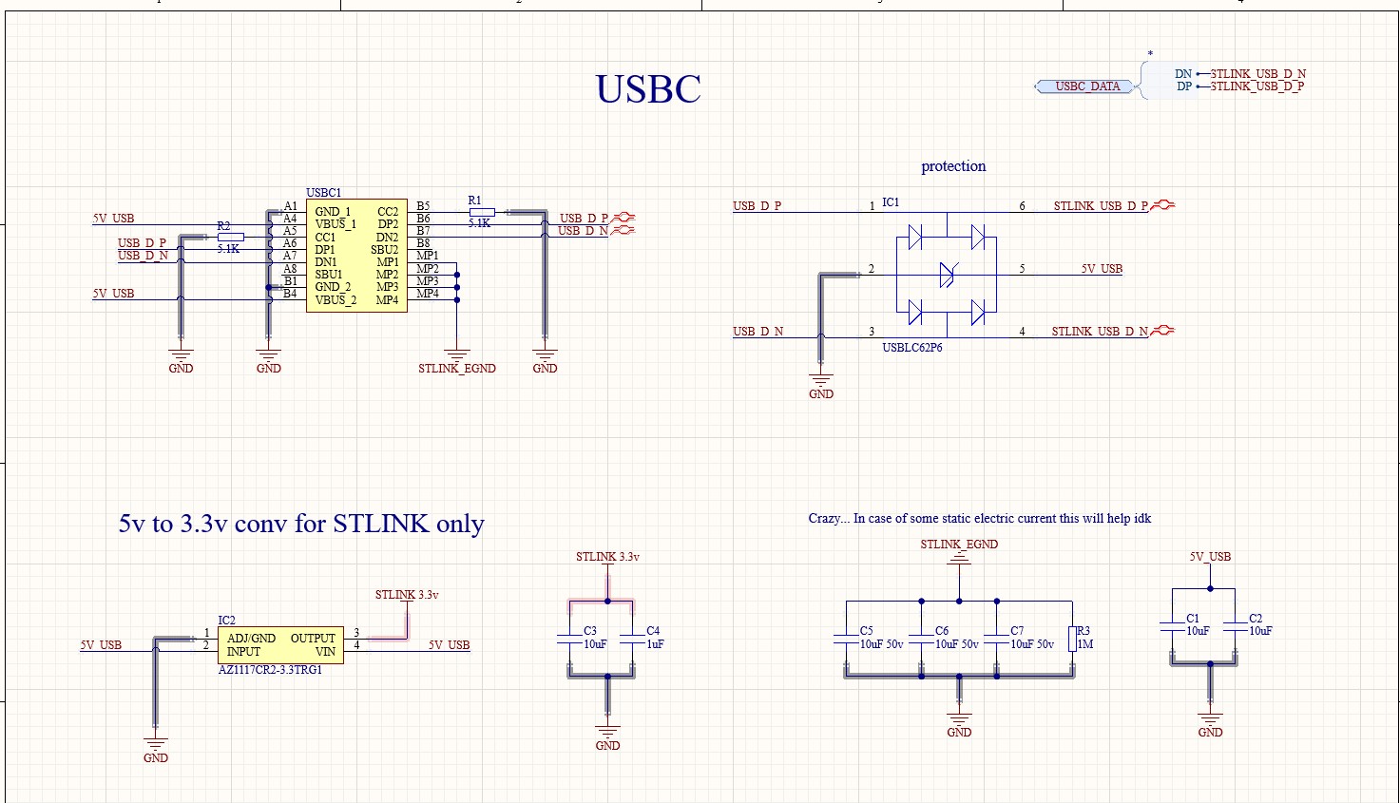
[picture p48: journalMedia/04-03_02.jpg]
usbc

**Total time spent: 6 hours**

# April 4: Good sleep = Good, new ideas and HUGE AMOUNT OF ENERGY!
I may have made gearbox holders in one day or may i not... I have experience tho (yes, i made them entirely today XD)
A lot of work done today:
 -Gearboxes
 -Interface board shape with more space for ICs
 -back sensor mounts

Im hungry now ;-;
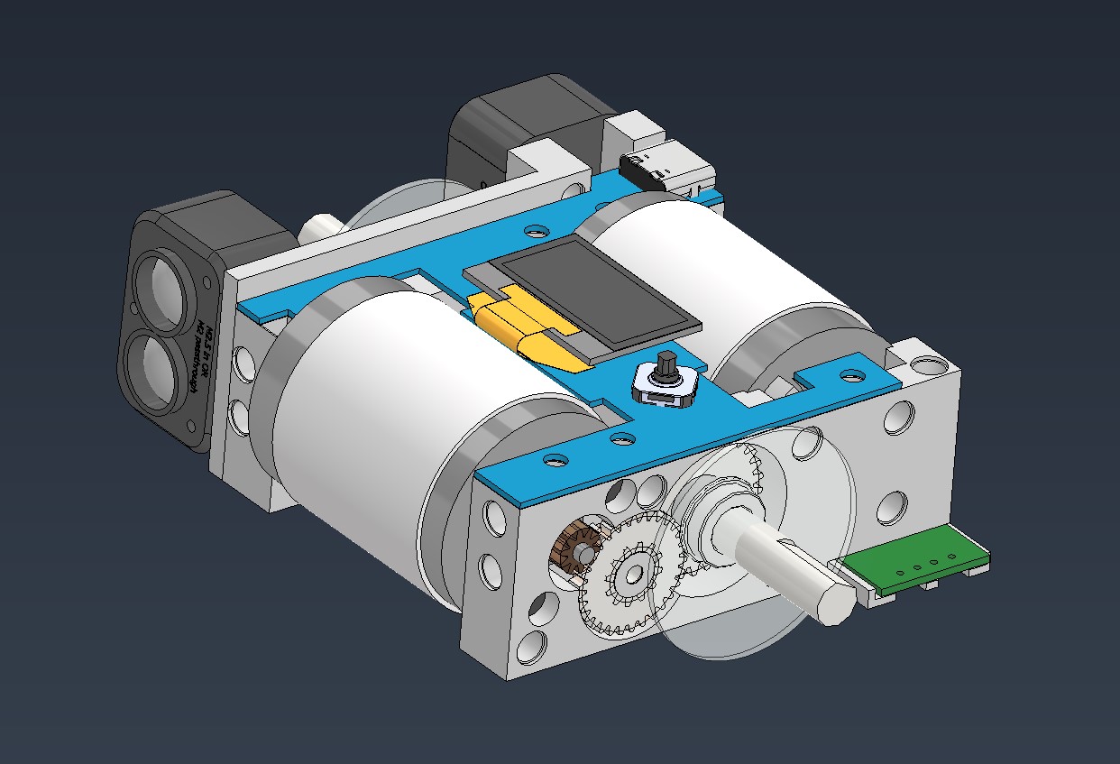
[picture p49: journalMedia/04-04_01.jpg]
gears

**Total time spent: 7 hours**

# April 5: Another day, another day...
Anothe day anothe day.

Today i made front mount... front face... Idk how to call it! It is a part which holds line sensors (no screws needed!), distance sensors, battery and the plow. I had to add place for wires inside XD

Also i learnt something cool today! You can see through parts with "section wiev"! Like now motors or gearbox dont inrerrupt me or i dont have to change visibility of certain object every 30 seconds

Also remember to angle you distance sensors, so they wont hit and detect ground! By brother came up to my room for something, and adviced me to do this. And i think is has a looot of sense!

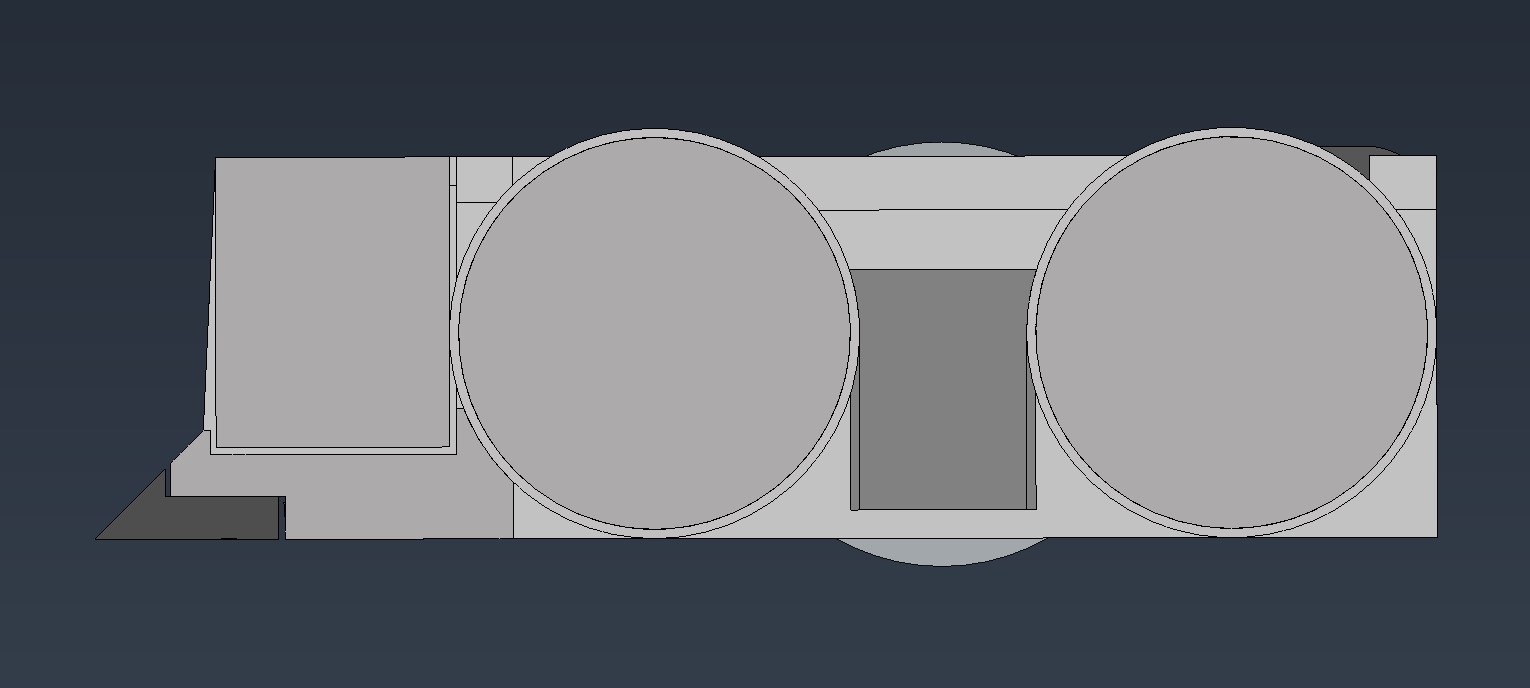
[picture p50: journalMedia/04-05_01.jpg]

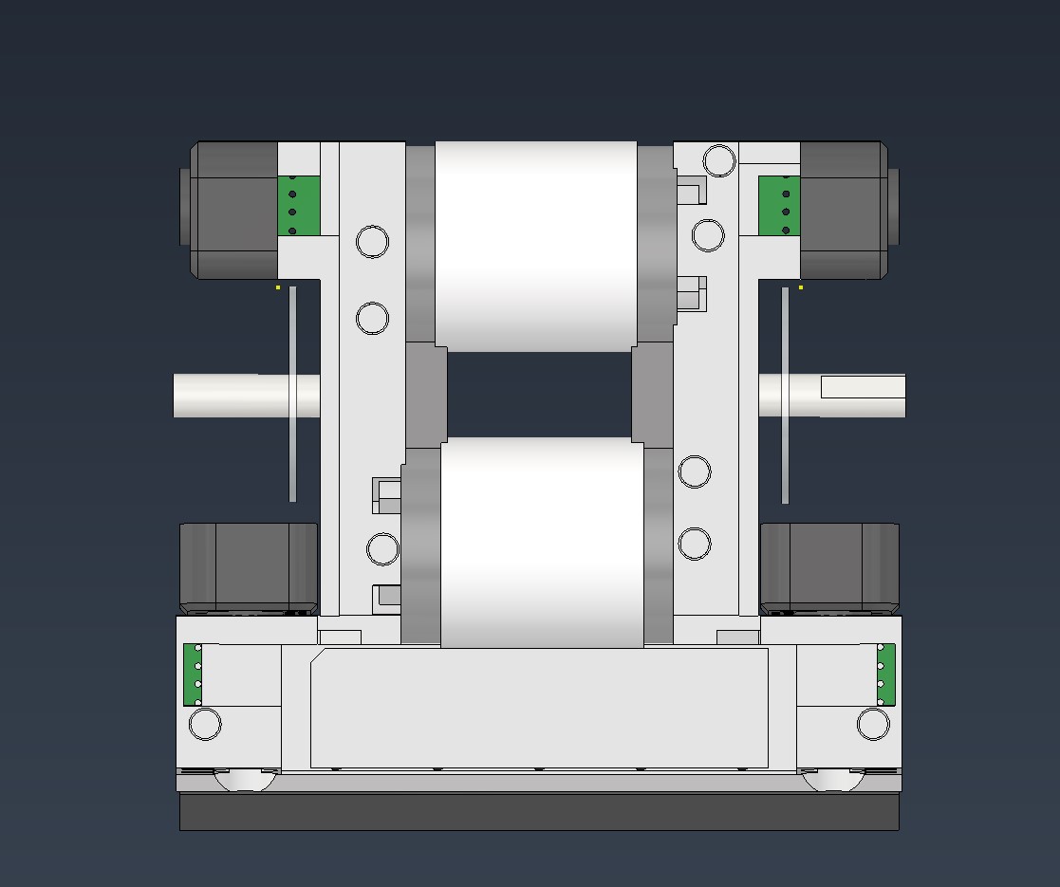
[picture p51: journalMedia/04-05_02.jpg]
cad2

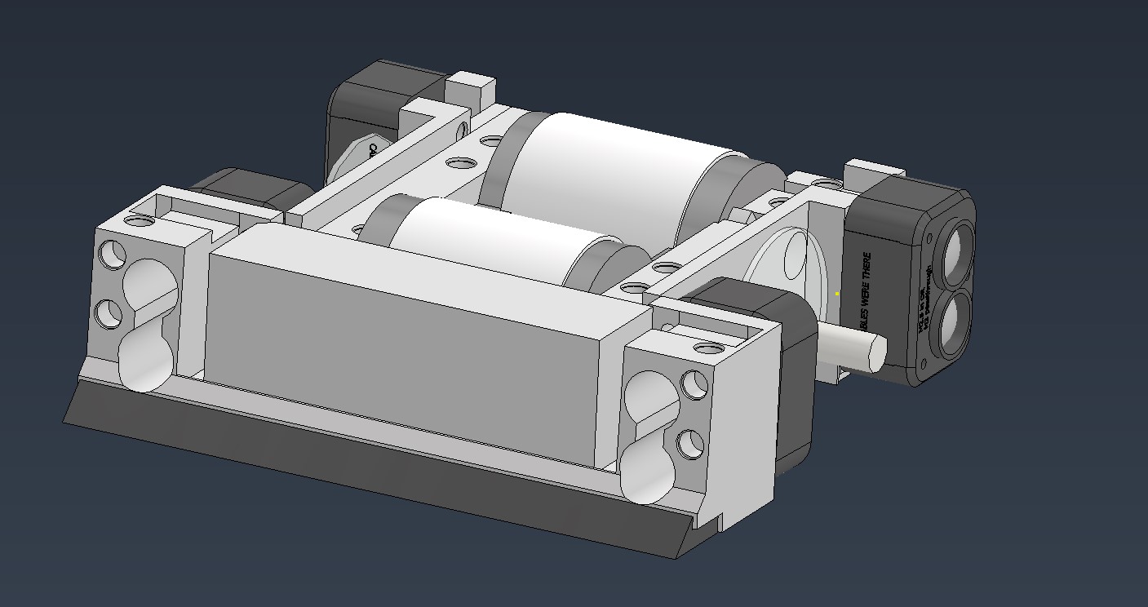
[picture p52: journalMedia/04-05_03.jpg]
cad3

**Total time spent: 6 hours**

# April 6: DA HELL
Guys what the hell. I want to change a few parts but i cant! I dont know what the hell happend in my cad. Could you help me?
I have a lot work to do for school's 3rd year project, so i will just do this today, and come back to CAD tomorrow.
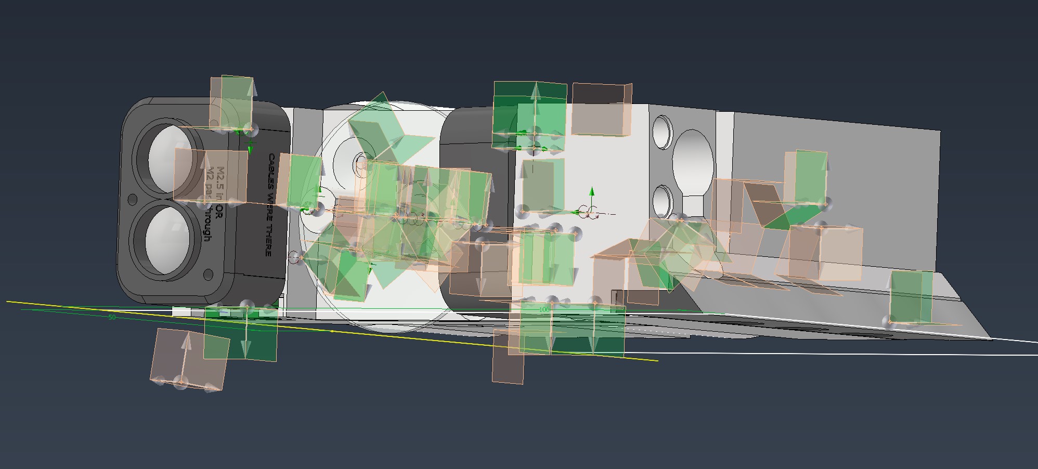
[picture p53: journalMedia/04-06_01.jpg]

**Total time spent: 0.1 hours**

# April 7: Front plow - sctrok plow
Today i customized front plow to my needings... requiements ;)
Also after beating and beeing beaten by cad for a while i managed, to make front mount adapt to plow. Like yk, i want to have longer plow, i edit its own base sketch, update assebly and BLAH! Now front i auto updated to plow :D
It made my work a lot easier thus. To achieve this i used something called "Project Geometry" which adaptively project geometry from some object into sketch. Also a lot of contraints to not break anything ;)
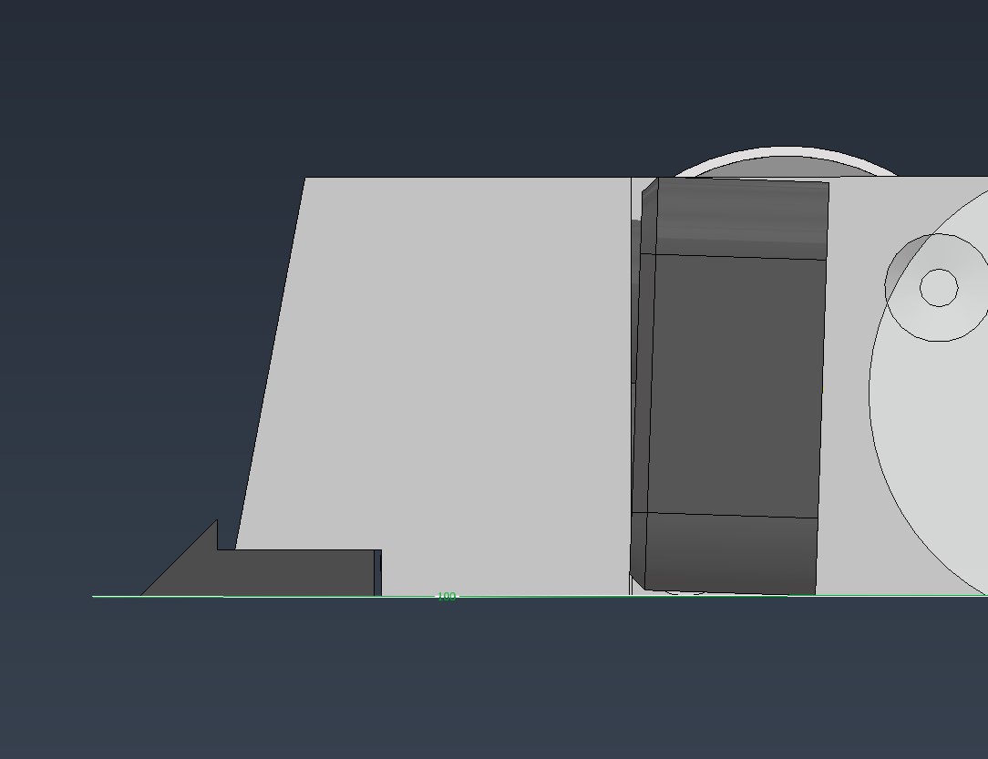
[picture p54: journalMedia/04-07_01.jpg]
plow type 1

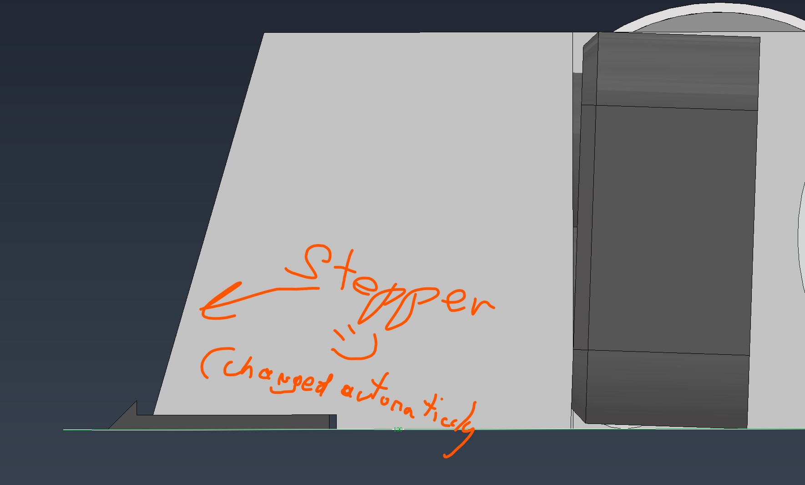
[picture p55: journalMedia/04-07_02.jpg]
plow type 2

**Total time spent: 2 hours**

# April 8: 3d model is done done done?
I think 3d model is finnaly done!
I changed my mind, and made plow, like, a loooot bigger. I want my weight to be at the front. If it wasnt my robot could do somehting like wheele, and we dont like it, beacuse it is easier to push me off if i dont have my plow on the ground. Inventor sais it is now about 50g inseat of 20g, so it is looking very good. Also i made ceiling, beacuse why not.
Adding cutouts in plow for line sensors was a little bit of more work - i had to tinker with dimensions and contrains a lot. After all i just YOINKED one hard coded dimension and this is now all okay and changes by itself to be okay!
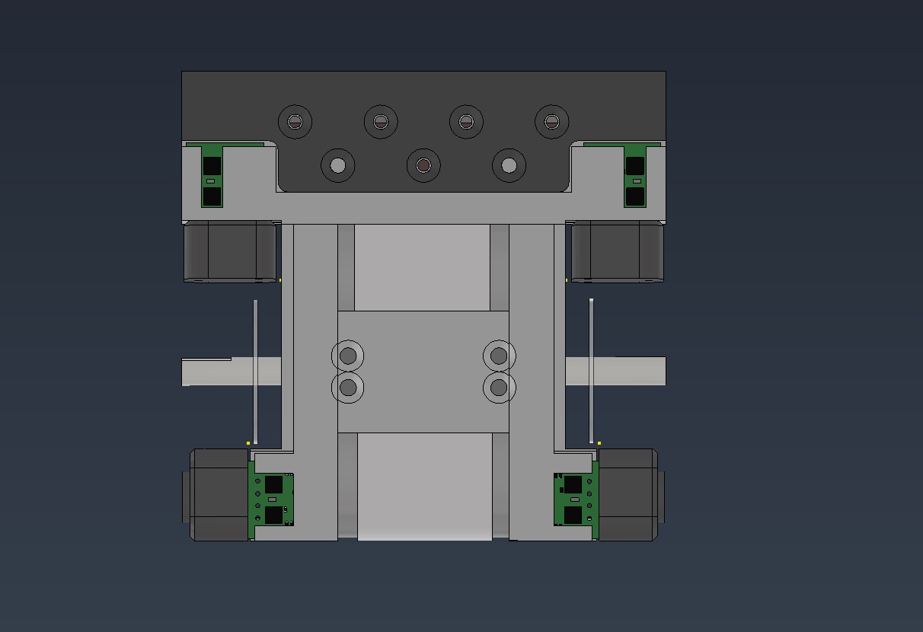
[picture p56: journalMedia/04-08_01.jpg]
plow

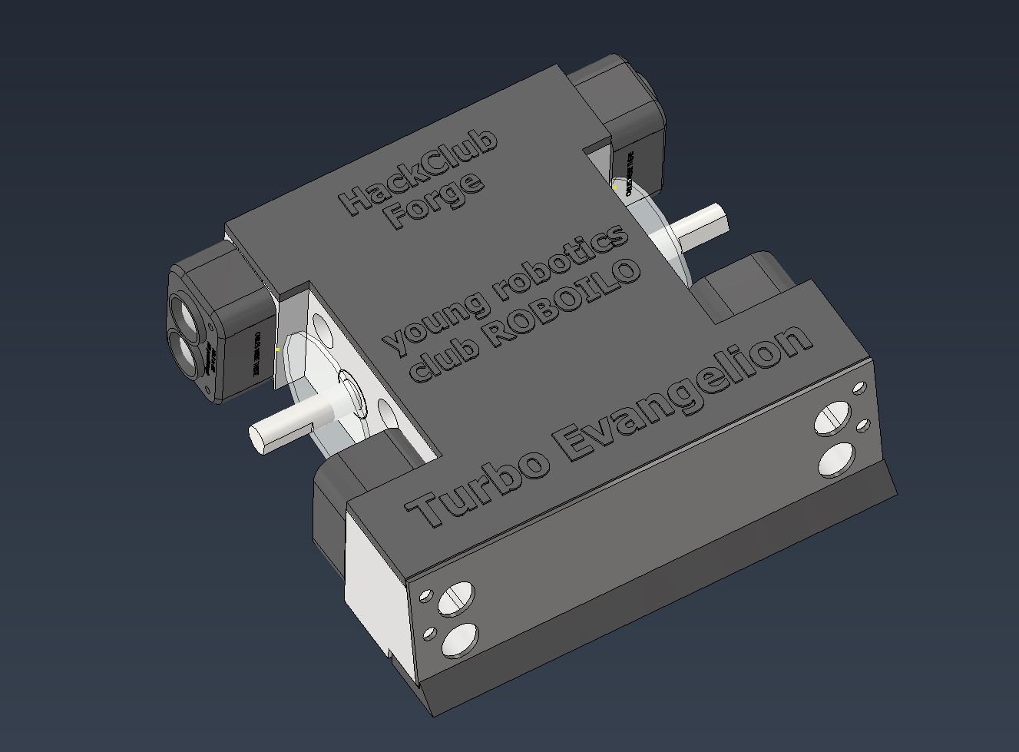
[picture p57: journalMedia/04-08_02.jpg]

**Total time spent: 2 hours**

# April 9: Sharpie Sharpie Sharpen?
I printed all of the parts in school, to test all of the fittments. Before printing, while i was tinkering with this PEI plate i came with idea of making front of the robot with something similiar, but more thinner and flexible. I think it will be very cool and sharp! I made quick sketch, we well see whats comes out of this.
After printer was done i assembled it and added insert. See image :D

...Thus i dont know what i will do with motors wire connectors ;-;
This is "my futures me" problem i suppose :D

PS. These are replacement motors from Evangelion, not these stronk ones i have found on aliepxress, for Evangelion Turbo. But they are in same dimensions so yk...
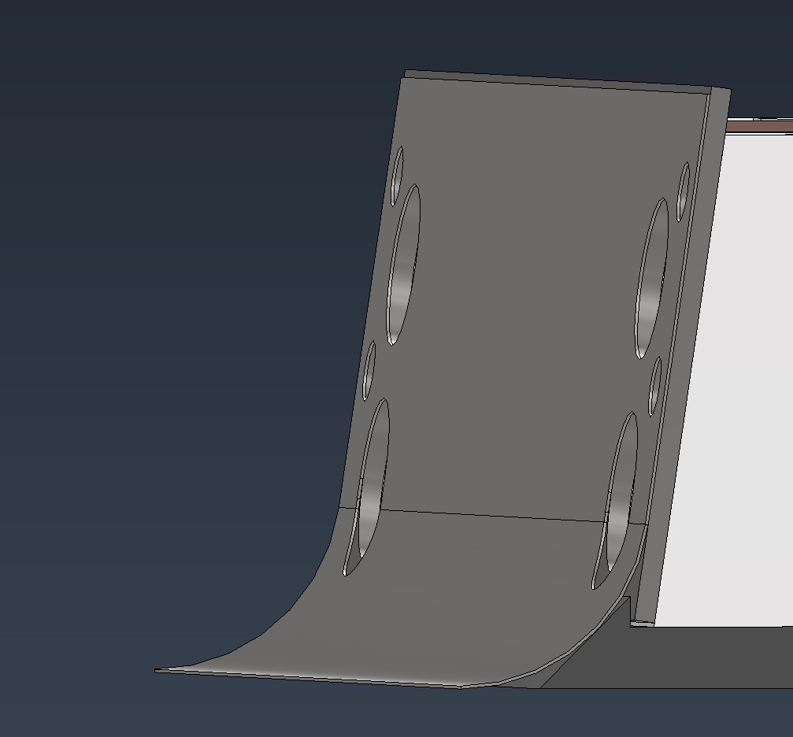
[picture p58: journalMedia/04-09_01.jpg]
springsteel

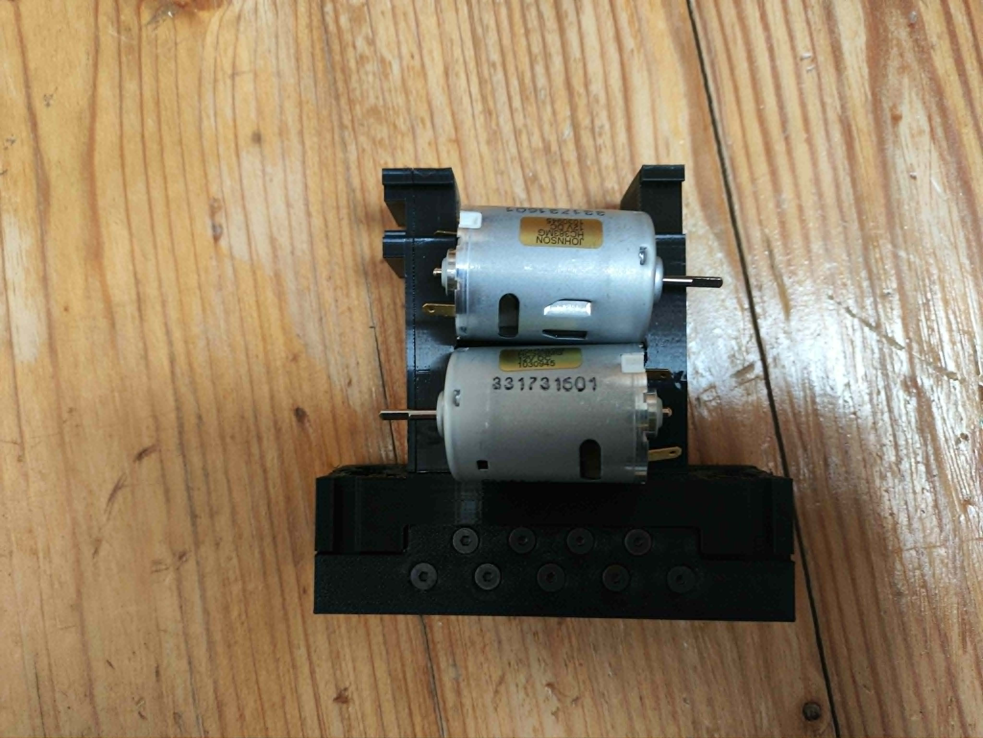
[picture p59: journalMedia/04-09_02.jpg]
3d printer parts! 1

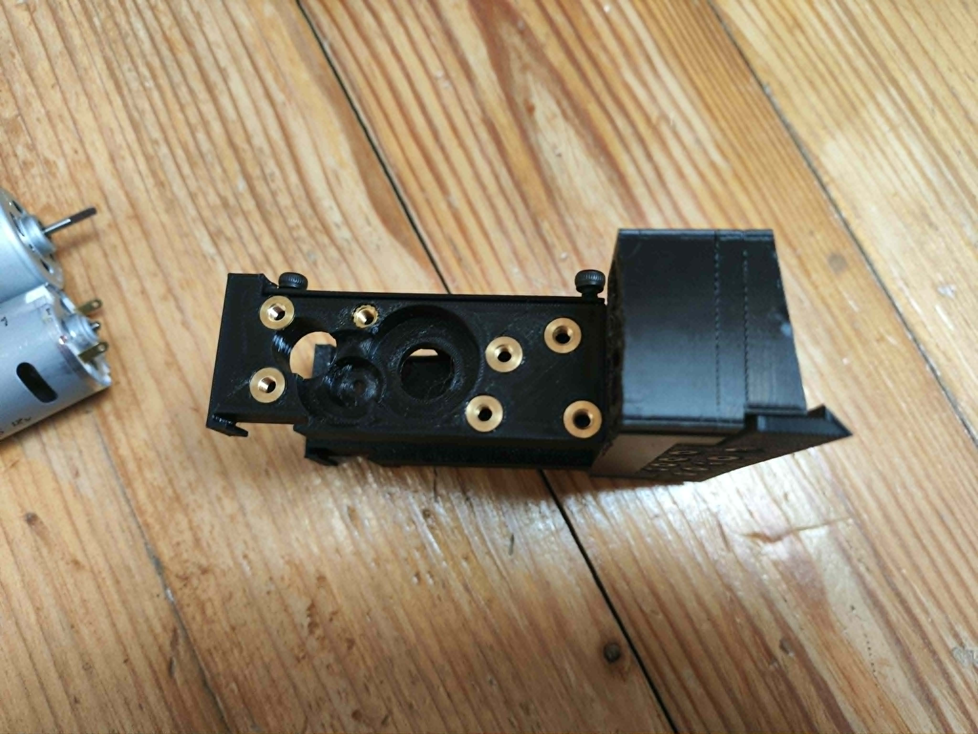
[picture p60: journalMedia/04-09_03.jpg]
3d printer parts! 2

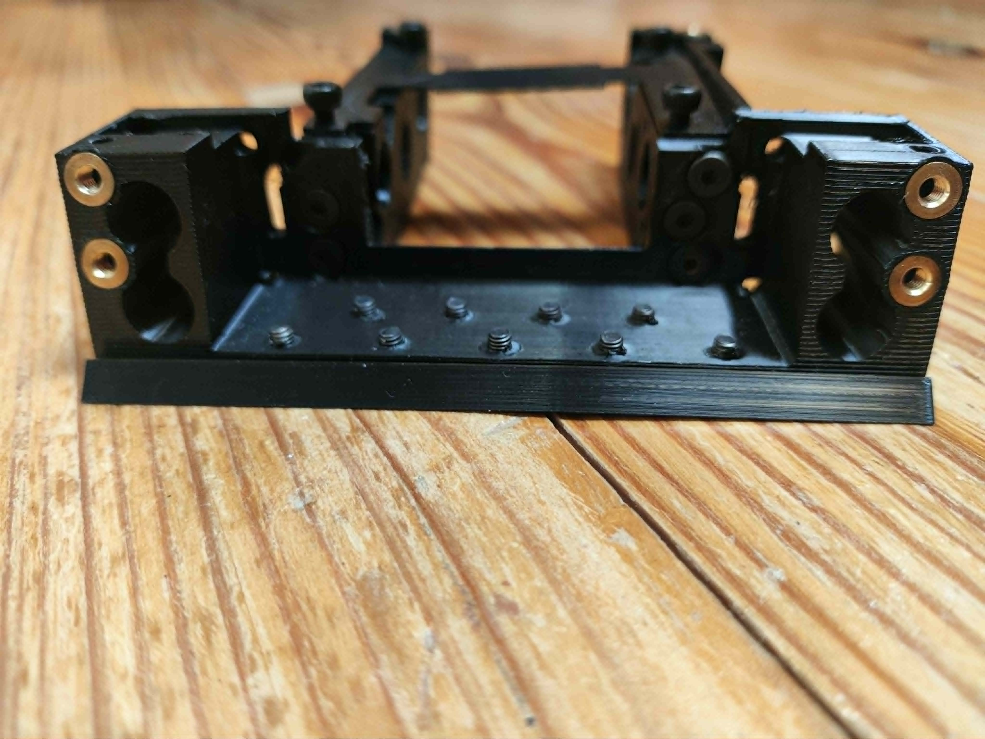
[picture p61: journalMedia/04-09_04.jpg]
3d printer parts! 3

**Total time spent: 3 hours**

# April 13: doom.
F... FFF... UC...
I realised thad 0mm of clearance is to small. I moved everything by .7mm.
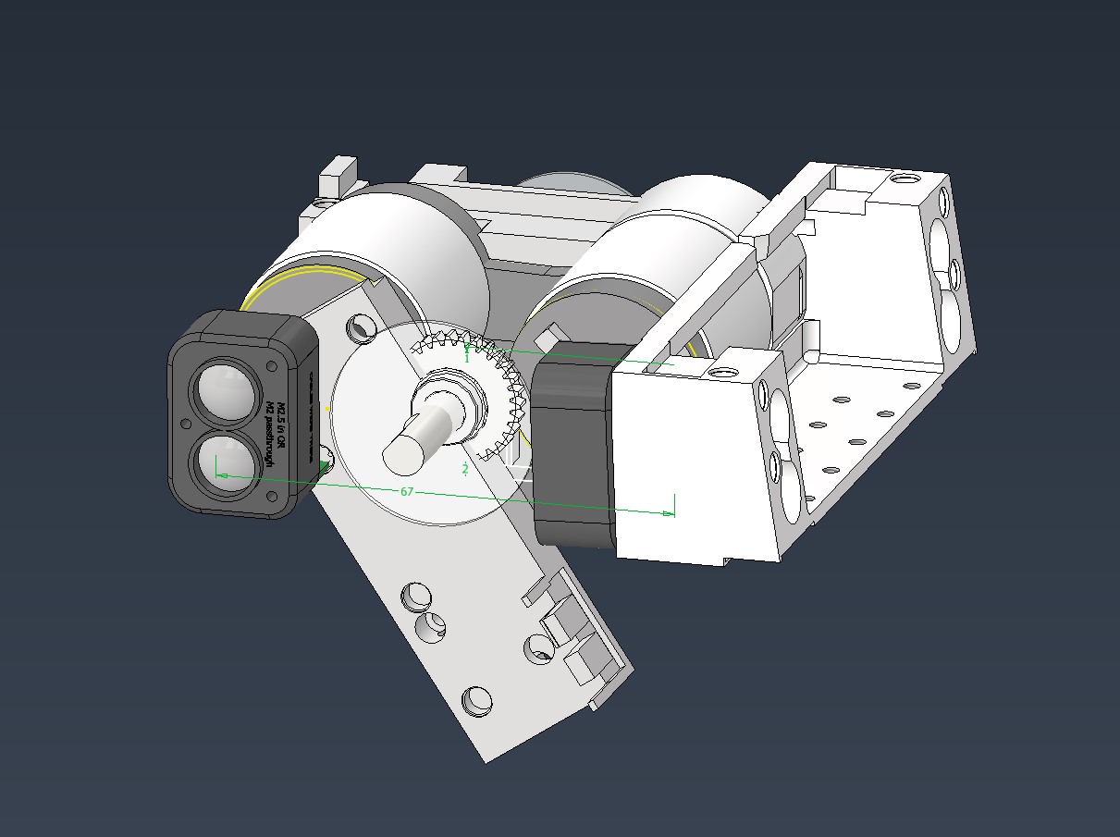
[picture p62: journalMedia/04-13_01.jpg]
doom 1

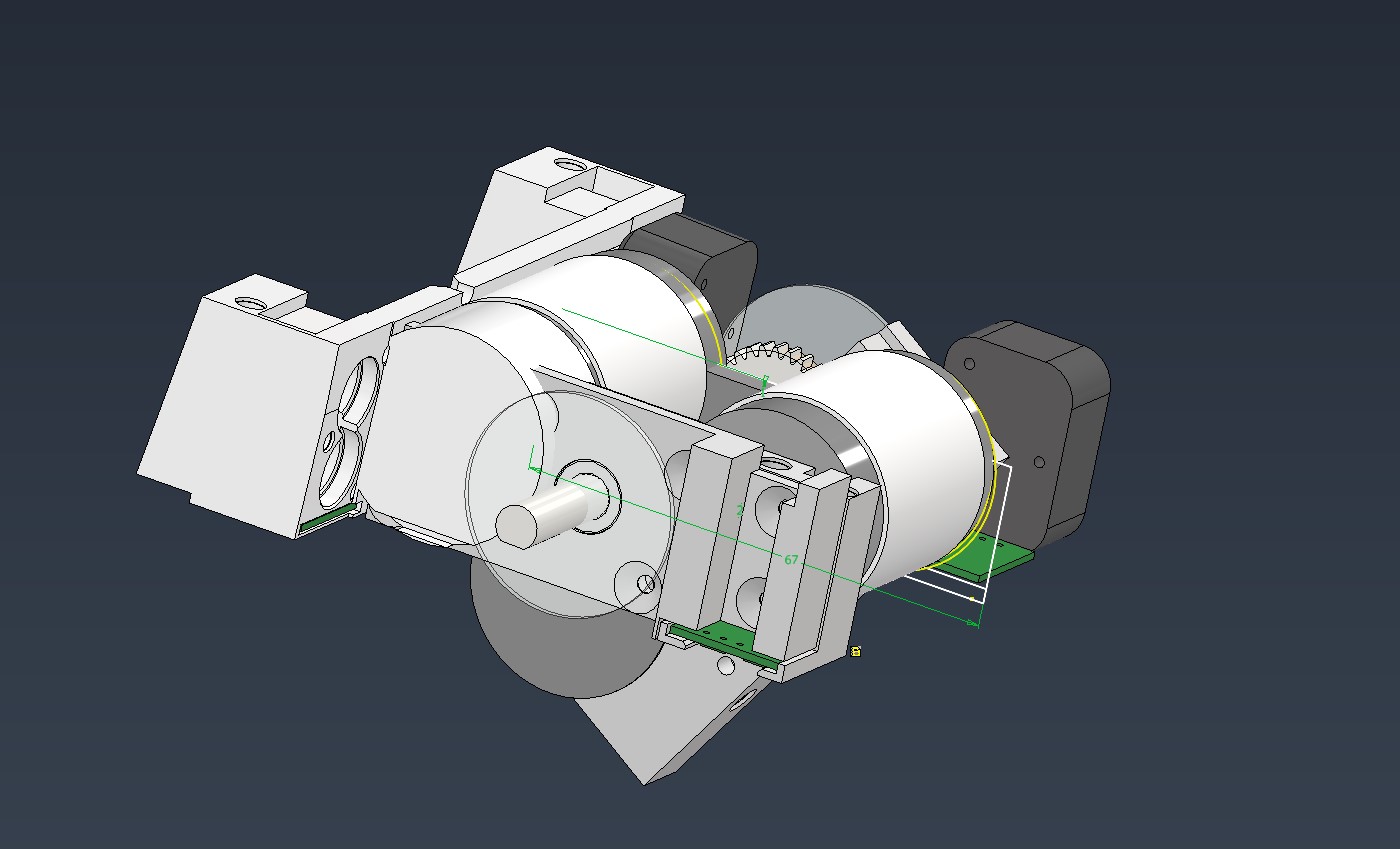
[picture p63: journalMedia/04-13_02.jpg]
doom 2

**Total time spent: 0.1 hours**

# April 14: We have our robotics club meeting today, so it okay :)
I talked about this with one of the students from our club and chatgpt. I was told to do:
 - Make a not-adaptive sketch in inventor
 - Make all extrusions you need from him
 - Make sure it all extrusions you need, no extrusions more after next steps
 - Go back into editing sketch
 - Now, project least geometries you need to make tou sketch fully stable
 - Change back to beeing adaptive
 - It shouldnt breake anything now, when you move something

This is very consuming way to do anything, but for me it works for now.

So... yup. I made gearboxes and front mount from scratch.

I have overall ideas and how everything should look like, so it took less time than when i was making everything for the first time
undoomed 1
undoomed 2
**Total time spent: 8 hours**

# April 15: Guys do you think this is a good idea?
I would have like 2mm *2 more space for routing PCB, on the other hand i risk shorting, like... *everythin*.
more pcb?
**Total time spent: 0.1 hours**

# April 15: PCB Interface
I changed and fixed few minor things is schematics.
It was tiring but i have all things arranged now. I dont know how i will route them tho XD

schematics
pcb
**Total time spent: 4 hours**

# April 16: PCB Interface
I spent my time at computer today reading JLC rules and guidelines for manufacturing PCB. Did you know, white and black soldermask requie at least .13mm? While other colors minimum space in only .1mm? This may make a big diffrence in small PCBs! I have my rules i made in repo ("MyRules" file). I also searched and found some smaller connectors, beacuse there is no way these JST 1mm i have put would work efortlessly.

JLC link to their site: https://jlcpcb.com/capabilities/Capabilities
pcbiing
**Total time spent: 4 hours**

# April 17: GUYS WHO LOVES COLD AIR!
HELLYEEE! Cold electronics = good electronics! Also now i have more downforce and grip (like 1g, but still).
I Also deleted few uninportant things from PCBs, like soft-latching button (ik its so coool, but i have no space on PCB... Its so sad...)

PS. Why the hell such small fan costs more than like 4010 fan? They want like 10 bucks for something this small.
I will search on ali, maybe i will find something cheaper thus.
SHHHHHHHHHHHHHHHHHHH
**Total time spent: 2 hours**

# April 18: METAL METAL (i want CNC in home)
A lot minor but important changes today! Biggest and most important from them:
 - I want all of my parts made from metal! (please CNC from JLC dont kill me with your price)
 - I made my own wheel HUBS
 - Updated all of the parts to metal
 - Front line sensors are now Screw-Mounted (No screw mounting is cool, but JLC might have a problem with manufacturing such thin wall - screw mount have no thin walls, so its okay)
 - Reinforced front a little bit - no obvious weak spots for now
 - Interface is now 2mm wider thanks to no gearbox cover walls!
model
hubs
**Total time spent: 4 hours**

# April 19: Motors motors motors... Drivers? I wanna bigger.
I think i have PTSD beacuse of Evangelion. His drivers (drv8251) are limiting him to about 70% of his max powers. AND to add into function his motors are... weak.
For this project - Evangelion Turbo - my most complicated robot i wanted to go with bigger drv driver, with inner MOSFETs. I though it would be enought. My friend, Michal, had put them in his line follower and it is driving flawlessly. Unfortunatelly i have PTSD. I think i need to go bigger. Reaserch, reaserch reaserch... DRV8702 - external MOSFTES driver. All of the current i need. I think it will be perfect, I dont know how i will fit it. We well se... Schematics done!
schematics driver
schematics mcu
**Total time spent: 5 hours**

# April 20: No chance, that i will route this thing and this will work at high frequencies...
I redone HUBS. Little flanges was added, to make wheel more stable.
I added and arranged nearly all of the parts on the PCB. 2 Layers will not be enought, which is sad, beacuse theye are cheaper... We well see.
hubs
PCB back
PCB front
**Total time spent: 2 hours**

# April 22: Will it work tho?
Its a mess. I decided to use one of middle layers exclusively for GND, middle layer mainly for VCc, top and bottor for everything else. Idduno men its a lot of work, thus not so much to journal...

PCB 1
PCB 2
**Total time spent: 8 hours**

# April 25: More time spent on PCBiing
More routing... Routing Routing Routing.

As a brake i changed HUBS, to easier shape and easier manufacturing.
Additionally I change aaalll of the holes to "screw", from shape of heat-set brass insert - like men, have you tried putting heat-set brass insert in metal? I have not and i dont like to.

Also guys! Never ever forget about you connectores! I realised today, that batteries *have* a XT30 connector, and theye are not wired *wirelessly*...

CAD
**Total time spent: 3.5 hours**

# April 26: Get the exorcicsts! For whom!? For me!
routing routing routing routing routing routing routing routing routing routing routing routing routing routing routing routing routing routing routing routing routing routing routing routing routing routing routing routing routing routing routing routing routing routing routing routing routing routing routing routing routing routing routing routing routing routing routing routing routing routing routing routing routing routing routing routing routing routing routing routing routing routing routing routing routing routing routing routing routing routing routing routing routing routing routing routing routing routing routing routing routing routing routing routing routing routing routing routing routing routing routing routing routing routing routing routing routing routing routing routing routing routing routing routing routing routing routing routing routing routing routing routing routing routing routing routing routing routing routing routing routing routing routing routing routing routing routing routing routing routing routing routing routing routing routing routing routing routing routing routing

pcb
edge
**Total time spent: 4 hours**

# April 27: Do you think it is done? Nah. Try DRC.
So uhm.. "Design Rule Check". Yk, this little think that tells you, that you silk mask clearence is too small on 53 elements, or your via-to-via distance should be bigger? Yup. I have more than 500 errors XD.
I fixed alll of them! Now, i think it is fully done. I am sending this to my robotics coach to check it, and i will come back with his feedback!
pcb
**Total time spent: 6 hours**

# April 28: PCB into model
If you didnt know you can export PCBs from you favorite pcb software into step files!
In footprint i have used 3mm bullet connectors, but i can fit only 2mm ones, sooo... BRUTE FORCE! YAY!

Now everything fits.

My little cute motor driver :)

CAD
CAD
**Total time spent: 0.5 hours**

# April 29: Guys i got feedback from my coach.
Hes an engineer and work at BTW so hes got the *knowlege*.
...
He said quote: "Hey, Szymon, If you told me you wanted spaghetti, i could order you one. You didt have to make on on you PCB"
...
Yieiks.
...
About good info, he advised me to use MOSFETS in DFN33, not 5x6 i curretlny have ("Its only 15A, not 100A, it will be okay"). And more important, to divide Mosfters and drivers and controll into something like senctions. Like yk, electric interference etcetra. Better driver.
I will work on that, but i think i will stick to 4 layer PCB, beacuse it is only like 4 bucks more expensie, but makes routing a loooot easier.

After all i felt productive and devastaded today, so i made some research about pricing and options in metal parts. I found out that CNC is hella expensive, but you can get BJ or SML parts for pretty good bang for a buck.
I will prob use JLC, beacuse i orded PCBs from there too
BJ example from JLC
SML example from JLC
**Total time spent: 2 hours**

# May 03: More testing!
After some break and spending time with my GF i am back!
My brother suprised me, he ordered for me one steel front! For the competition i will need to orded few more, theye are very prone to braking.
After tapping aall of the holes and assembling it i had to change:
 - Gearbox covers - walls (im afraid of shorting anything) and clearances to gearbox
 - Gearboxes clearances for bearings
 - Place of holes for the laser distance sensord (bruh, they are all wrong XD)
 - Updated battery model and the xt30 connector
 - Changed front mount so i will have place for connectors from battery etcetra
 - Add place for cables from front sensors
 - Back steel reinforcment plate
 - Made front more steeep, yay!
 - Aaalso Im thinking about burring whole *spring steel* front idea

So uhm... After my coach told me my PCB is trash, i had to redo everythinkkkkk... WHYYYY..
This time i used smaller mosfets and payed SO MUCH MORE attention to clarity. Im sending it to my robotics coach now, we well see what he will say.
Also i found and used a few smaller components, like smaller quartz or bullet connectors (2mm instead od 3mm ones).

HELLYE! My brother agreed to print my parts on his ender (thus  only most important ones...)!
It will be junk, but not junk enought to test!
prototyping
PCB1
PCB2
printin!

**Total time spent: 11.3 hours**

# May 04: Is c0 an better idea?
After consultation with my coach we came up with idea of using smalle, stm32c011 MCU and using UART instead of CAN as communication.
I have remade PCB and schematics. While working i discovered that C011 is so much smaller, BUT it doesnt have DAC. Quick search on DIGI and i found some DAC on I2C.
So in SUM:
 - UART for communication with main MCU
 - HSE crystal
 - Debug serial wire
 - Gpio input NFault from DRV driver
 - 2*PWM output for driver
 - 3 ADCs for Temp, battery voltage and Current readout
 - I2C for DAC.

So uhm. After i made it i think about switching back to g431... After all it is more capable MCU and why not... Also can is better for noisy scenarios like meine.

Guys. I scraped changes. I thought why not if i already took the effort to put bigger MCU here? Its like 1 bucks diffrence and i got full CAN now!
I really wanted to do galvanic isolation, but i didnt manage to fit it. BUT. I organized texts and even added hackclub forge (guys give us bitmaps of your logosss)!
I think i am really done here and i can start with main controller pcb.
mcu
schematics
PCB
**Total time spent: 7.1 hours**

# May 05: CANing and Schmatiing
So after all of my effort i had to rewrite my schemtaics... yay..?
Thus i have like 7 pins left on MCU so its okay :)
Anyway, guys! Remember! To connect signal ports (these big blue ones, not small yellow ones) you HAVE TO USE signal harness! Not normal wire. I spent like hour figuring out what is wrong XD
Discovery came by mistake.... Yeah. It is awful. But i think schematics are done!

So uhm... Another problem. Annotation. Tools-Annottaion-Board Level Annotation. Here you can change how altium annotates, reset and re-annotate all components...

THE HECK! JLC WANT LIKE 70 BUCKS MORE FOR .15MM VIAS XDDD
I had to change everthjinnnnn

Thus... I think i have cooked today. I dont know how i will route this... But yk. TO BE COOKED OR COOKIN!
overall
cubeMX
PCB XDDD
hello do anyone read this?
**Total time spent: 9.9 hours**

# May 06: Burnout?
Today i have worked most of the time on main controller PCB. Yk some routing some parts placementr etcetra...
Yesterday evening i came up with few improvments for the 3D model.
I changed them to!
here they are:
 - Added holes to rotate back distance sensors to add space for cables if neccesarry
 - I added some place for thrust bearing in gearbox - we well se if it fits tho, beacuse it is tight fit 
 - Added a looot of fillets to make easier assembly
 - Changed fan mouting - now it is screwless. also he have little guard for protection now!
 - Chamfer for screw to go in!

I also think about adding buzzer to main PCB. We well think about that later. Thus i worked not-so-much i started feeling burned out... 
So no more work for today! Im going to sleepover with my friends and chill out with some board games!
Have fun guys but dont forget about your mental health!

fan guard
**Total time spent: 6.6 hours**

# May 07: Eat Sleep Program Design (spent some time with friends and came up with good ideas in meanwhile :)) repeat!
Beacuse we are going back to school tommorow, after holidays i have to do homework and accually learn for exams... This is saddd like yk i cant spent half a day in CAD.
Yesterday when i was at sleepover and my thought was wandering i got worried about one things. And this is accualy question for anyone who is reading this.
Do you think this is an issue? Or smth like that? Or with good lubrication it wont couse any issues?

*Im talking about this flange bearing and middle-sized gear. They have 0.1mm of clearance... This part of flange bearing is statics - it doesnt move of anything like that...*

Yeaaa... I lied... I didnt to all of my homework. Thus i have rims now!
I accually have *some* experience in custom wheels and rims. First of all, silicone is like a gel - it wont go throu .1mm hole or anythink like that! Rule of thumb is about 1.5mm minimum radius for silicone to flow throu. 
Secondly, it is really hard to pour silicone into mould when mold and rim have 1mm of diffrence in diameter! So keep about 3mm of "offset", without anny additional things to make your future life easier. So uhm... Experiment, try and learn guys! And remember, always wear protective gear! This thing *may* cause cancer for you futere self!

*Simpler the rim, the better the wheel... i guess... Thats how my brother used to say* Thus idk how my schools printer will be able to print it :)

So yeaaa... I lied agaid... Instead of doing homework i found smaller mosftets and made reverse currect protection. I had to delete all of the tracks from MCU, then move everything up a little bit and reroute everything back. Idk why altium is so bad to me... Thus now i have reverse polarity protection!

fan guard
sketch
3d
mosfets!
**Total time spent: 2.8 hours**

# May 08: I had to get up early to school. Such a shame.
Im tired. But it is wekend now!! I think i will have done PCBs in a week or so!
Today i routed few things, changes few things in 3D model. Also researched and checked price on JLCCNC. It was horribly expensive ;-;
Cames out, that mills accually exists and have *some* diameter. That why you need to add internal fillets when you design something for CNC! Bigger the fillet, smaller the machining time, lower the costs!
I managed to bring down price from about 150 bucks per plow to 35 bucks per two! (they were about 50 bucks for one so it is like... pay 50% more, get one free deal, so not bad).
Thus it was not a lottttt today unfortunatelly.

Also screw holes were in diffrent places from holes in CAD lol

pcb
cncmill
JLC
**Total time spent: 3.8 hours**

# May 09:OMFG MOM LOOK, THAT ME!
Thanks guyssss!
me
**Total time spent: 0 hours**

# May 09: *Clap calp* **TUDUTUDU Wake up Daddy's Home!** (thats my vibe nowwww!) (if anyone didnt catch, thats an ironman reference)
Yeah guys, i think i accually didnt explain one thing before. Low pass filter on ADC sensor lines and URAT lines. I use them, for analog signals, to not get messy and distorted by high freq nearby signals like PWM, uart, buck conv, it is just cleaner for MCU! There i use about 10k cutoff freq.
"Wait, if low pass filter is used to negate quick changes in signal, using it on uart wont make it junk and unusable for mcu?" Yeas, unless you use configure it to have veeery high cutoff frequency! I used about 500kHz cutoff here.
Normally i dont use low pass filter for uart, they are just not needed. But Beacuse of space saving im routing them *under* buck converter, which is just fast switching thing, so it generates a lot of noise. Good thing is that this noise for my buck is in 1Mhz-2Mhz spectrum,
so as i  said beffore, i added 0.5Mhz cutoff low pass filter, to cut off this noise! My uart is running 115200 baud, and chatgpt told me it is about 50kHz, but for signal intergriety and other electric shieniegasens you need about x2 to x10 higher cutoff freq, to not distort clean uart!
So put 30ohm and 10pF here.

As a thanks for picking me out, from all project decided to add buzzer, to annoy everyone i can think of :)
And one more IR receiver for start ir controls. (For sumo robot you want all of them - more ir receivers = lower chance of **not** picking out referee signal to start sumo fight).
And i made these small PCBs for rised ir recivers today

Also 4pin 1.27mm connector i found was discountinoued so i had to search for another one lol.
I found some 1mm ones, at the competition i willpray that they will not desintegrate and fight.

Mire routing and squeezing everything...

IR receiver on rised schematic
IR receiver on rised PCB
controller
**Total time spent: 9.4 hours**

# May 10: Ah yeas, the price of working too long last night
So yeeaeaa... It was as productive day as yesterday
Today every signa line got routed. Tommorow will be power lines.
New quick tip for you! Dont route fast signal lines near eachother (for example UART neart I2C, urat TX very close to uart RX, SPI to i2c, like every possible combination) (exception is ofcourse differentail lines like usb (d+, d-) or can (can high, can low), beacuse theye are like veeery noise resistant).
Thus why may you ask. Beacuse of electric interference. One quick changin wire near second one quick changing wire will make them both super duper noisy. Nobody like noisy signal. Analog signals dont care about it, beacuse they change greadually, and slow.
Thats why, i routed uart slightly apart.

I also exported PCB into cad (File>export as>.step) to check if i made any errors while settings boards shape, check holes aligment etcetra.
And yeah, it is lookin HELLA SICK!

Ceil too :)

routinggg
hellye
ceil

**Total time spent: 8.9 hours**

# May 11: Capabitiles of manufacturing ;-;
I checked JLC design capabilites, specially for vias. When i read it last time there was that vias need to be .3mm hole and .4mm diameter annular ring, so i followed that.
After reading it again i saw it... They can do .3/.4mm via BUT preffered for them is .3/.45mm (and bigger annular ring)... I had to change every via on controller and drivers .-.
Hellye... I guess...

Also i routed power lines!
And... Somehow ground...
Yeah, always remember to use Design Rule Checker to check you work.

I changed vias to pad in power microswitch - i done this beacuse im worried, that it myght short circuit on my metal gearbox lol.

GUYS I DISCOVERED NEW COOL THING!
Shift+S to get into cool one layer view mode
Then ctrl+shift+scrol wheel
This way i checked if i had any overcomplicated traces or vias which shouldnt been there!

Bcool thing
microswitch
BURN THE WITCH!!!

**Total time spent: 6.6 hours**

# May 12: Final touches and we are done!
Guys! I cooked so much!

Final touches, few disconnected GND lines, more than a few (lol) disconnected signal, overall cleanup.
And ofc ANNOTATIONS!
Remember to annotate! IT is sooo muchh easier to solder if you have good annotations.
And another important thing, annotate your connectors - add text for these gnd, power and signal lines (right beside connector) - you will not have to open you laptop to crimp these connectors in the future 😃

Additionally i spent some time on reseach on MOSFETS. I want one that are capable of high current with little-to-no power loss - beacuse power loss means HEAT!
And more heat equal more bad. Also i learned that if you use enough inneficient mosfet, it can desolder itself from PCB and cause big mess lol

In the qucik dinner breake I talked with my brother and he gave me some feedback! Here it is:
 - Check LDO footprint (it varies a lot and wrong one can couse a lot of problems)
 - Remove dead copper (more copper = more heat capacitance, BUT more dead copper = higher capacitance of traces so it is worse)
 - Straighted lines from EPROM (i2c is fast and dont like suddent changes in direction)
 - Bruh, low-pass filter on TX near MCU? The heck? - Yeah, it wouldnt work. low pass filter filter noise, but i put it before any noise was added to signal. nice.
 - Also i had to fix some power lines, beacuse i made GND tight necks lol (less space = higher resistance = higher noise and more heat -> So it is bad. We want alll of the space for comeback of GND)
 - Plated and non-plated vias ;-;... I had to fix them!
 - Also to make then (PCBs) in one chuck so it would be cheaper to order! - like yk, connecter all of the pcbs into one panel and order them as one pcb, cheaper!

*Indeed these cat annotations are abslutely necessary*
front
back

**Total time spent: 5.4 hours**

# May 13: JLC!
So If you want to but 3d printer parts from JLC, it not ADD>PAY>RECEIVE. Its more of sending them files, they rewiev it, then you send new version, then they may approve it or add another 60 bucks to you overall costs and then finnally they make it for you...
Yeah. Lesson for future me and all of you guys. It is a lot more work than i thought lol. Also always check your manufacturer capabilites. One more thing that came up unexpendictally is that they can do sharp edges - like lol, it just 45 degree mill and go brr, nothing crazy.
But the edge has to be dull, minimum of .5mm. Pretty sad, that i will have to sand a lot of material and blackening. Also i had to add little things, so they wouldnt complain (i had .5mm wall and their minimum is 1.5mm), to sand off later.

*I spent about 3hrs on thing freaking thing (isntead of sleepinn), but i think it shouldnt taken into time of improvment of this project, so i only journaled time accually spent in CAD*




**Total time spent: 1 hours**

# May 14: BOM and ceil!
Today i checked actual pricing in JLC and updated the bom accordlingly.
Also finnaly i had some time and motivation to make the ceil propely, and not quick and dirty way! (photos included ofcourse).

Qucik tip time!
If you want to extrude you image in inventor:
 - Convert it to black and white only (no gray, please)
 - Convert your image to SVG - beacouse we want vectors! (smth like https://convertio.co/ works)
 - ~~Use some webpage to convert it to dwg~~
 - ~~Open fusion 360 or autocad~~
 - ~~Nevermind... Accually open oneshape lol~~
 - ~~Import your image in SVG format~~
 - ~~Save file~~

NEVERMIN GUYS IT DOESNT WORK BUT I FOUND IT - I FOUND WEBPAGE CAPABLE OF CONVERTING SVG TO DXF.
https://cloudconvert.com/svg-to-dxf
Go check it out.
I spent too much time searching how to do this, so here you are :)

Also one cool thing i discovered is that you can group parts of you sketch with "create blox" - with that part of your sketch act as one.

*Pretty things took a lot longer than expreceted...*

ceil
katze
ceiling!

**Total time spent: 4.8 hours**

# May 26: Long break lol
Soo yeee... I started thinking about writing some simple code... But i have a lot to do at school right now lol.
I opened editor to adjust MCU configuration and i messed up badly lol.
Also yes i fixed MCU configuration where i could.

Always check your PCB before you are done with it lol.

mcu1
mcu2
cube ide

**Total time spent: 0.8 hours**

# May 27: I accually started doing something beacuse of streak system LoL
Retook images from CAD and Altium, polished readme, made proper BOM in .csv format. 
nothing serius. Just beeing consistent :)

Added BOM in .csv format and BOM section to readme.

Accually i took a look at some readme's and change mine.
credits for inspiration: https://github.com/notaroomba/cyberboard/

Also guys remember to have everything separated by "," and not by ";". I had to repair bom beacuse github was mad at me beacuse of it lol.
Also my github is tweaking...

mcu1
bom

**Total time spent: 1.9 hours**

# May 28: Research day
Not so much. As far as i want i will have massive pill of the code for this robot, so i wanted to do some multi-file programming thing.
Today i researched a bit about this, global variables, local variables and everything that sounds complicated lol.

Some nice page to read, about global variables and when they are acceptable: https://sqlpey.com/c++/when-are-global-variables-acceptable/
I think this is basic, but very important, for multi-file design: https://codelucky.com/c-multi-file-programs/

I still have to do some deep research on headers, beacuse they sound complicated and unecesarry for me, for now...

research

**Total time spent: 0.6 hours**

# May 29: ~Printin~!
Nevermind. I accually work same as before, but now i journal every small step, that i was like "meh, only 20min of work, i am too lasy to journal this.".
Now i actually journal this lol.

I changed a bit my distance sensor mounts/holders and printed them in school, so i wouldnt have to worry about them in future!
3dmodel
printed

**Total time spent: 0.3 hours**

# May 30: Coding - start (first time using lapse... lemme know if link is accesible guys)
I never thought i like coding, but now i think i hate it lol.
I started by adding multiple .h and .c  and after thinking for a while and coding some other things i deleted them lol
I dont know how i will use them if i cant use variables from main. Writing function could be my soution, but we well see in the future.

One thing i wanted to point out is how i choose prescaler and counter period for timers, which are used to generate PWM signals for drivers.
Bigger freq = less noise, less torque and lower "speed" and more, a lot more EMI! Lower freq have unfortunalety more noise, but dont generate as much emi as higher ones. 
On the other hand going much lower than 20-30Khz can lead to very bad noise which you may hear (humans hear from 20Hz to about 20Khz) and unstable torque and speed of the dc motors.

*Also writing code for hardware i dont have yet is pretty hard. I cant test and write code in the same time. If i would write whole code now, and then get some errors, debuging this would be crazy.
[Im talking about hardware problems, STM32 is pretty...  whimsical lol. For example my oled wasnt working at my old robot, beacuse I2C was... too SLOOW. Like whattte helll]*

Oh and i would forgot. I added OLED libraries to my project! Guys, if you want to use oled, please do it the right way. Use DMA or interrupt, now polling. DMA and interrupt is soo much lighter on cpu!

Alsoo i got into measuring load of the cpu... Which comes out to be harder than expected lol
Like in the MCU everything works how you set it up... Unless it cant, beacuse next interrupt comes before end of the last one.
I have written some code - will test it and fix it in the future, when i will have hardware. Now i cant even check it lol

Guys my lapse... I have too slow internet for lapse for now. Network provider said that they will fix it by last friday. Yesterday the exceeded expectation and send another info, that they will fix it by next saturday.
Currently im trying to work on my phone hotspot but it is painfully slow lol

*Aarav please dont sue me for not having lapse while coding, it broke while i was trying to upload it😭*
ioc
code
lapse
error
timer
how i feel

**Total time spent: 3 hours**

# May 31: RAAAGHHH I CANT WORK IF LAPSE ISNT WORKING AND IM TRYING TO FIX IT INSTEAD OF WORKING

Laps freakin not workin. I also posted in lapse-help channel. Raghhhhhhh!
beuh

HORRAY! I managed to recover lapse!
I managed to recover yesterdays laps and make it smaller and faster! At the start i set stoper and at the end i also show it so i have about 3hrs and a few minutes lapsed :)
Video file is right here: "journalMedia/05-30_67.mp4"
Video file

*lol, it came through, i didnt believed that github would allow this lol*

*------------------------------------------------------*

Today we are doing research on how to clear signals from sensors - kalman filter, median filter, moving average etcetra.
Im trying to use lapse in google chroom instead of firefox this time, we well see if it helps and works now!

Best video of kalman filter i have found: https://www.youtube.com/watch?v=HCd-leV8OkU
This has a lot of information too: https://www.youtube.com/watch?v=jn8vQSEGmuM

After research  i think i will stick to ADRC or PiD in this robot. Kalman would be cool for IMU or predicting opponent location but it is hard and complicated!
research

Lapse link for todays research: https://lapse.hackclub.com/timelapse/bxvmavSPl1Jg

**Total time spent: 1.5 hours**

# June 01: Sending for review!

After quick thought process and qucik talk with my brother i decided to ground all of the metal parts and motor encosures with 1Mohm resistor and 100nF capacitor.
I am worriend that without this i would die of EMI lol

Also double checked everything before submitting. Wish me luck guys!

*have a nice day fellow rewiever :)*
emi

**Total time spent: 0.5 hours**

---
title: "Evangelion Turbo"
author: "Szymon Filipkowski"
description: "Evangelion Turbo is an SUMO robot of footprint 10x10cm and weighing less than 1kg. It is direct successor to my last robot, Evangelion. Evangelion have 4 distance sensors, 4 line sensors, IMU, oled, UI and maybe even enkoders (idk if i will fit them tho)"
created_at: "2026-03-16"
---

# June 01: Chamfering!

Okay, so today i designed and 3d printer very helpful thing for chamfering (first photo). Beacuse drilling anything by hand is very, very hard thing to do straight.
While it was printing on our schoold mashine i prepared and cleaned all of the fronts and back and the ceil. 
While i was chamfering got to know, that you should chamfer aluminium in veeery high speed! Beacuse it acts like bubble gum to you drill in lower speed, which results in bad and innacurate holes. 
I got like 60 holes to drill, chamfer, clear, chamfer again and then clean in alcohol that i lost my mind lol.

*I chamfer everything, to hide countersunk screw all the weay in - this way i can have more robot in my limited 10x10cm footprint*

I tried polishing to flat 3 of my parts, but beacuse of lack of proper sandpaper it comed out horrible. 
*Polished surfaces may or may not reflect and confuse distance sensors of the opponents*

As for the sensors, drilling mouting holes and cutting orginal mounting *arms* (idk how theye are called lol) was not hard, but a precise job.

Also one more quick tip!
When you drill use drillin oil (or just any oil, even water) - it helps to achieve clean cuts and clear holes!

Heres photos!









Also i found out that my MCU stm32g431 have been sold everywhere... as well as all of the normal replacement - so i have gone digging.
And to my suprise i have found something! stm32g491 will work lol.
*most important pins for compatibility arent gpio or any other connector but rather Vcc, Vss, clock, BOOT0 and nrst - with them wrongly connecter you will either kill your mcu or it wont work at all!*


**Total time spent: 7.2 hours**

# June 02: Im cooked lol

Today i cut banana plugs to exact dimensions (always wear protective gear guys!) and broke my PCBs.

Uhm... I ordered only 5 of them from JLC...

I wanted to heat them to 230 degress, solder plugs and a *a lot* of capacitor, wait a while and be happy. Something broke and now i have shortcircuit on battery lol.




Also i forgor, but i made some research on the way to school, (about 1hr in the bus lol) about IR filters.
Halogen lamps may disturb work of IR TOF sensors, so i thought about adding them.
From my research i concluded, that i want narrowband filters at 850NM, which will cut every other spectrum of the light that i dont need - my lidars work with 850NM, and narrowband filter will cut everything below 850-30NM, and everyhing above 850+30NM.
Theye are not cheap but i think i will give them a try.

Lapse:
https://lapse.hackclub.com/timelapse/hRIpPztWr8to

**Total time spent: 2.5 hours**

# June 03: Solderingggg

Im coking with soldering main controller PCB.
I got scared of destroying motor drivers so im focusing on controller for now.

Tip for today: use flux for soldering, dont depend only on tip (soldering iron? soldering thing? idk how to call thing you solder with, im not talking about the tool, im talking about this usable thing on spools lol) - it makes life easier and soldering a looooot quicker and more precise. 
Also it gives nice look.

Unfortunetaly i have bought some wrong components which i have to buy...
Some zener diodes in wrong casing, some resistors which i forgor.

front
back

Lapse link:
https://lapse.hackclub.com/timelapse/dXYIZFRqisLL

Actually i soldered MCU (i started doing it at 22.00 o clock), beacuse i wanted to check if everyting was okay. It was not. I didnt start lapse bcoz i though it was quick 20min job lol.
So i have shortcircuit on my mainboard, so i took another one and solderem LDO and MCU into this...
I have 1v instead of 1.8v on Vcap and core. I will try to fix it next day.
At 01:00 AM i got finnaly to sleep with more issues than before lol.
**Total time spent: 7.5 hours**

# June 03: I should have bought PCBA lol

*Yea... I got camera working for lapse!*

After 4hrs of debuging i managed to connect to stm32cubeprog withg diffrent computer.
It comes out that i had too log USB cables and it didnt work lol.

IT FREAKIN CONNECTED HELLYE!
*Beacuze of all the mess i dont have any way to connect my camera lol, maybe i will find to change it into internet one, it is some xiao esp sense c3 that i won at some competition*

BRUUUUH...
my controller, which is based around stm32h5 works while beeing connected with like 3cm cables to voltage maker, but using proper cables with Crocodile connectors not works.

So today i managed to connect to the mcu. But nothing else lol.. *Kill me plyz stm32h is so complicateddd*
cam
pcb

Lapse link:
https://lapse.hackclub.com/timelapse/elWAS2NwqL74

We got another late nite session lol.
I managed to connect to PC propelly. It comed out that i had micro-short-circuit between 3.3 and boot0, which caused MCU to stuck on bootloader and never boot to programm...
It was hard to find out, beacuse this shortcircuit wasnt really short circuit, it had about 5kOhm resistance! Combined with 10K pulldon, there was about 2.2-2.6v on BOOT0, which is high state lol. 
**Total time spent: 11 hours**

# June 06: Evangelion Turbo edit incoming?

@Leo dmed me on slack, asking if he could use my proj for his edit... Im kinda curious what he will cook.
I added some filets, deleted few thing, made a few things more pretty and sent him step file of the project!

*Im looking forward for you edit leooo!!!*
conv
step. 
**Total time spent: 0.5 hours**

# June 12: Comeback after short beake!

Parts from JLC finally arrived!
I opened box and carefully inspected for anything which may be wrong (this costed shitload of money)

Also i weighted everything for future use and writed it down into excel!
Disasembly of current prototype was also a thing, i weighted, like everyhing lol.

Why? Beacuse i want to be exacytly 990g - 990g in 1% accuracy weigh is exactly 1kg, which is maximum i wanted.

*My calculations from excel says that this robot will weight 890g for now, that is okay, thus not what i really wanted*

I also made little 3d printed thing for chamfering, beacuse last one didnt work well lol

Imagesss!





**Total time spent: 2.5 hours**

# June 13: lock the heck in

Okay so today i locked in onto making metal parts usable and accurate, beacuse dimensional accuracy in SLM parts is pretty poor!
I sanded everything that i didnt want by hand (photos before and after), chamfered according to proj.
Also i rechamfered my front and back plates, beacuse theye were not straight lol.

My front plow is made from #45 steel CNCed which is pretty hard! *Guess, who said "yeee, its only half of the milimiter, i will sand it by hand, no problem" and cant sand it now, even with sanding mashine...*

I wanted to tap everyhing but i broke like 4 taps... *I had hard, very hard, time removing broken bits from holes*
Thankfully i managed to tap all plastic parts before!

*Quick tip for today!
Tapping, sanding, drilling, always use oil! It sound weird to use something slicky, but trust me it works lol. It helps to keep your tools be cool and live longer and it is a loot easier to drill!*

Imagesss!









**Total time spent: 9.8 hours**

# June 14: W grandpa

He found M3 tap for me! *I broke it like 40min salet :sob-emoji:*
Also my brother found M2 tap for me! *Yup, also broke it, 10min later :skull-emoji:*

I tapped all M2.5 on all metal parts, and all M3 on front mount... Then i felt that this is easy and i understand it now LOL

Additionally i broke like 4 drills on these 1mm holessss... Using new HSS drill bit was the key. *One bit stuck inside, and i had bad time taking it out xD*

So the key for doing geat taps and dont braking them inside your part, is actually PID tuning. You have to tune yourself to be gentle and dont feel to good.
Go little, like quater of a turn, then go back same quater turn... Go and back... Stop and go. You will learn this someday!
*AND OFCOURSE A LOT OF LUBRICATION OR OLI!*

Imagesss!







**Total time spent: 5.7 hours**

# June 15: Again in school robotics club!

Hellyeeee! In the morning i bought M3 taps kit, with 3 stages. First stage was easy, i could do it even with hard dril... I broke all of the 3 of them.
Fourtunetaly i managed do tap all of the m3 holes in hearboxes befora that lol. I also borrowed (i knowrrr, agaainnn) M3 tap from frien... WHICH I ALSO BROKE LOL

I should be laughing but... These shish material is so freakin harddd.

Also i tried sanding front wedges on the mashine, which shjould be easy. Guys it is only .5mm... right?
Is is not "only" .5mm. It is .5mm of frakin hard steel! I burned my fingers like three times.

After all of this i tried to get tap out from hole, from the other side with screw.. You wont believe it. i broke it also LOL

Imagesss!






**Total time spent: 5.2 hours**

# June 16: Parts!

Second batch, last one, of electronics parts finally came!
It was MCUs, drivers, mosfets and other similiar parts, so this was more expensive one...

Alsoo i just wanted to share how comediacilly smally are these connector lol
I ordered 30 of them (i need about 17 for one robot, but yk, i can broke while soldering, theye are small and hard to solder), so i ordered 30.
Chinesee guy only sent me 10... Hope they will arrive until competition, or im cooked.

Imagesss!
*.6mm jst connector next to m4 screw*


**Total time spent: 0.2 hours**

# June 17: Lock in again day.

It was funny and a lot of work today.

In the morning i cleared silicone form (in our robotics club), made silicone and poured it into. I wanted to go for nice purple color, by mixing pink with black, but they came up grayish...
Later i started working on assembly but... It wasnt quite rigt. My screw i got were .1mm to large (i used longer ones from diffrent batch, with right tolerances), bearing were broken (i had to hammer them out, and hammer good ones in).
A few days ago i broke screw inside, so i tryed cut it in half to get it out with "-" screwdriwer... I countld so i just sanded it flat. I also had to sand my SUPERHARD CNC MILLED FRONT WEDGE WHICH WAS SUPER HARD AND TEDIOUS BEACUSE IT IS FREAKIN SUPER HARD... *thankfully it fit*
And ye, i nearly broken my electric screwdriver, which i got fo christmasss...

After all of this, finnaly gearboxes were done. One was spiinning okayich but other one was not. Thats bad, it is only 7.5:1 so it should spin like butter. I think it if bearings fault, but i had to go home so i could fix it then.
Also pretty suprising, but tolerances on SLM on right gearbox and left one are pretty driffrent. Like left one is loose and right one - i had to drill a lot of holes beacuse it didnt fit.

When i was trying to force gearboxes to run normally, it started to smoke from somewhere... I think i have burned out motors :skulk:

*Additionally i emailed some local filament resselers to see if they would sent me some free samples. Aaand cutified readme :)*

Imagesss!









**Total time spent: 7.3 hours**

# June 18: I just want it to work already >.<

I started day with getting wheels out of the forms (wait, actually i checked, theye are called mold in english lol, sorry). It was messy, but after clearing, they comed out nicely.

I soldered everythin what was left (ye, small .6mm raster connectors too) to the maincontroll. Eveything worked... To the point. After soldering eeevyrhing but bullet plugs... It just borked itself. I got 0.23ohms of resistance beetween 3.3v and GND.
FREAKING AGAIN! I didnt do much. It was only soldering bullet plugsss. When i apply current it heats up under MCU, but it i think is okay... This shish hars is.

I got one board left, idk what to do to be honest. I can solder it but i dont have these small connectors on hand, beacuse chinese guy sent only 10pcs, not orginal quantity. And i need about 17teen for this board lol. Not funny, nevermind. Cryout.
I didnt even ate dinner beacuse of that.

Wait i got one idea while returning by bus home. I can use some smaller connector and one electrolyte cappacitor, insteal of two chunky bullets plugs (may this be the problem in destroying eveyrhing inside pcb, we well see).

So yea. I actually started lapse in the morning, about 8AM, but it got totally borked while i made 1hr break for my sanity and qucik ice cream (GOD I FREAKIN LOVE ICE CREAM). ye, it sucks.

Imagesss!









**Total time spent: 8.4 hours**

# June 19: Physicz in like magic

I asked for help my robotics coach, Patryk, via messenger. Next day (which is today) he took his warm-camera (idk how to call it lol).
I soldered directly into 3.3v line, beacuse short cicruit was on this like (about 0.22Ohm from 3.3 to GND, about 20K 5v to GND, about 100K VCC to GND -> shortcircuit somewhere on 3.3v line).
Current limiter on bench power supply to 2 Amp and here we go. After some searching one line lit up clearly. In altium i search and it was 3.3v line, so there was something bad happening *at the end* of this trace.
After mooore searching and *crying* we found a little too much of solder under my 'lil connector.
AND THAT WAS IT! IT WORKED AFTER I REMOVED CONNECTOR AND THE PROBLEM! SCIENCE IS OUR MAGIC GUYS!

Also i emailed PCBWay if they could machine front wedge for me, beacouse one i got from JLC is far from perfect...

*Im spending my time, workign at our robotics club at school, and i have my camera set up at home, so no lapse :sob:*

Imagesss!

**Total time spent: 1 hours**

# June 22: Work work work work work

PCBWay said that they will partially fund me my front wedge! Succes!

Today i soldered more components, and checked again for any FREAKIN SHORT CIRCUIT. There were none, so it is okay :)
It work like a bliss. AND IT LOOKS SO FREAKIN COOL BABBYYYYYYYYYY!!!
*Soldering these small zener diodes beetween MOSFETS was so freaking hard lol.*

After cooking with main controller (it looks so freakin cool!) i started working on one motor driver.
Why only one? Beacuse im worried about breaking it or cooking it on solded plate. So ye, cookin cookin cookin!
I have done most of A side, tommorrow next side and shitty connectors which i hate <3

Imagesss!




**Total time spent: 7.6 hours**

# June 23: 10.00 to 19.00 with two half hour breakes. Nice. One hour spend on troubleshooting my younger robotics collegue robot lol.

Today i fully soldered one motor driver! It was tedious but here we are! I had some problems with random shortcircuit, but i hotaired a few things, desoldered mosfets and DRV motor driver, soldered new ones and now it is all okay!
I didnt have time to connect it to PC and test it, but all of the status leds are on so i praise to be okay and workin.

Next i soldered silicone wires to motors (silicone is better at disspating heat and more heat resistant than PVC or other wires. Also It is easier to manage and SO SATYSFYING TO TOUCH. And easier to solder).
And sanded by hand motor mounts, beacuse cad i okay, irl is sanding :)

For tommorof i plan mostly assembly, silicon insulating eveyrhing around motors and soldering two more motors drivers.

*these small connecotr are PAIN IN THE FREAKING ASS to solder*

Imagesss!







**Total time spent: 7.0 hours**

# June 24: Batch work(out)!

As of yesterdas "one motor driver is working", today i have done two more motor drivers, but i didnt test them(yet)!

Most chellenging thing was little connectors and diodes.

After soldering i tried assembling robot a bit and it looks so freakin cooooool!

Imagesss!






**Total time spent: 6.1 hours**

# June 25: I start to burnoout

So ye... One motor driver is working! While other one not. I resoldered mosfets and mcu, drv driver and CAN, nothing worked, i soldered new mosfets and new mcu, new drv and new can - still no good. So i just ditched it into "i will take a look later box".

AND FINNALY I ASSEMBLED WHOLE ROBOT FOR THE FIRST TIME! It looks SOO FREAKIKNG COOL!
Also our robotics coach told me it loock good :D

After going back home from long work i got aliexpress package with taps! I started tapping my M2 holes for distance sensors, but like 3 of them broke ;-;
A lof of cutting, sanding, cutting, getting burned i recovered one broken tap tip, and other one i just sanded dlat and a lil bit more. I want to put some PETG here and melt heat-set insert into this.
We well see about that.

Also i feel very burned out today...

Imagesss!





**Total time spent: 8.9hours**

# June 26: Helpdesk

Today i spent most of our robotics club day at helping other with their robots and eating pizza! Thats why this is such low timestamp here.

I assembled whole thing again and soldered tiny tiny cables into all of the front sensors. I added some hot glue to act as a strain reliefe, so i would snap pads or cables by mistake! Additonally hot glue is somewhat good insulator,
so i wont short anything on metal parts. After that i started programming and checking configuration (.ioc) file, but i could get anything to work!

*shortie shorie, not so long, we had end-of-year ceremony today. We celebrated with big pizzas!*

*Tommorow im going to lake nearby, to help rescuers as a volunter (no money for me unfortunetaly :( ), but im going to chill out there a looooot!*

Imagesss!


**Total time spent: 2.7 hours**

# June 27: Quick!

I wanted to get more wheels, so i had to 3d print rims! Model i designed before was perfect for SLS, but terrible for FDM so i changed it a bit.
I deleted all of bumbs and other thing that would cause problems for my brothers ender 3.

If you are casting you wheels by yourself (like you got your silicone part A, silicone part B, mold, mix them, wait, etc), then you have to have one thing in mind:
 - Silicone dont stick to any glue well, so you have to add bumb/hold yo your rims. Anything will help. On smooth surface silicone will just spinn. Most of the time it is grippier than rubber.
 - Rubber stick to glue well! You can skip anything uneccesaryy here! You can print flat/smooth rim and glue it later! It is easer to pour and grippier in *some* scenarios than silicone.

Imagesss!


**Total time spent: 0.5 hours**

# July 04: Comeback!

Comeback in breaking taps! I broke 4 today. This metal SLM from jlc is pretty hard lol. Beacuse of that i designen plastic bracked to hold back distance sensors.
Ah yeas, i would forgot, my connector arrived, i soldered them, and started assembly, as well as lubricated gearboxes :)

More assembly, soldering, wire cutting and soldering. Im cooked with wires, they dont fully fit :skulker:

*I was tapping in my grapnda workshop, so no lapse for that*

Lapse: 
https://lapse.hackclub.com/timelapse/Wfvlu2ybgLXT

Imagesss!








**Total time spent: 9.5 hours**

# July 05: 3dp!

I designed and 3d printed hold for drivers, beacuse i coudnt fit wires yesterday!

Imagesss!


**Total time spent: 0.9 hours**

# July 06: Works!?!?

Today i rewired everething that would eat more than some power (battery, motors) with smaller AWG cables, beacuse i could fit orginal ones lol

Later i actually started it! And nothing broke! Controller and one motor driver connected to stm32cubeprog like a charm, but one looks like to be dead...

After trying to code something, while nothing worked, i found out that i have some problem with external crystal... I just bypassed it and decided to use high speed internal one. For now nofith more broke!

Lapse: 
https://lapse.hackclub.com/timelapse/XehMPpMb8ODr

Imagesss!




**Total time spent: 4 hours**

# July 07: Programming

Helloooo

Today i started seriously programming. I could resolve problem with clock but idk why i have 3.3 on 5v line lol, still, i did normally connect to MCUs. Weirdo.
My oled dont work, beacuse i messsed up the footprint... I added one random pad inside. Fuck...
Not good Not good. I tried forcefully soldering it while skipping one pad... but it work out horribly lol.

Ah yeas, and i have written most of the code for motor driver.

Also i cleared out and fixed few minor things in schematics of pcbs.

Lapse: 
https://lapse.hackclub.com/timelapse/ypU_1K0k5lqW

Imagesss!






**Total time spent: 7 hours**

# July 08: Go go go go power-rangers

Helloooo

Today dones from todo:
 - Get buzzer to working
 - Program distance sensors (get them to work faster, 250Hz instead of default 100Hz) (made some shieninigans, and now i have one big function to which i gave RX table, TX table, UART handle and it works like a charm (i could do this in before robots lol))
 - Literally it was so much work, but i made them work!
 - Good filtration for all data from distance sensors (their temp, distance, strenthg of reflected laser, moving average filtration for all of this)
 - Got all of the ADC to work fully autonomusly, with battery voltage readout too!
 - Made full initial routine for robot

 Also i got hold up on new rulebook for upcoming competition!

*Also later i searched up for some smaller alternative motor driver and MCU, for v2 version! I think i would like to fit one big motor driver into one small PCB, we well se 'bout that. I have found upcoming stm32c532 FREAKIN small mcu. It got CAN, 144HZ and poretty powerfull cortex core, and DRV8701 in same package. It would be so freaking small, BUT! But.. but... butt :3... but the MCU ist out yet lol.*

*Ah yeas! i would forgor! I got shortcircuit on TX line on uart! I fixed in quickly and it works like a charm now*

EDIT: AND I HAVE WRITTEN QUICK SCRIPT IN PYTHON TO CONVERT DEC TO HEX, BEACUSE WHO ON THE EARTH WOULD USE DECIMAL IN UART COMMUNICATION

Lapse: 
https://lapse.hackclub.com/timelapse/t728XH_6cTbH

Imagesss!




**Total time spent: 4.5 hours**

# July 09: Holy **not** 67

Helloooo

FUCK. I bought 3.3v buck conv instead of 5v one. Thankfully it arrived today :D 6767676
I soldered it into all of the PCBs. got few shortcircuits in a process, but i got them out.
Later i tried to start CANning (yk, i CAN, beacuse it it spelled CAN, not CANNOT!) and i got huge problem. Some weirdo put NC on my schematics, where it should be Vdd for logic level :skulker:
So... ye... i got fucked up. Thankfully i have like .2mm wire in insulation and microscope lol. Here we go guys! Lets wire this thing up. 
ANOTHER FUCK TODAY! WHYYYYYYYYYYYYYYYYYYYY. I got shortcirtuic on 3.3 and gnd. WHY TODAY GUYZ; after desoldering components from PCB... it come up... IT WAS FUCKIN MCU. Blyat... 

OH YES. I forgot, but i have crosser CANH and CANL lines on motor drivers xD
I think i will order V2 version of PCBs in the future!
But ye, resoldering these tiny cables was paaaaaaaaaaaaaaaaaaaain in theeeeeeee assssssssssssssss.

Lapse: 
No lapse, i forgor :(

Imagesss!








**Total time spent: 5.3 hours**

# July 10: WHOA

Yeeee!
Today i desoldered mcu, sodlered mcu, desoldered mcu, had crashout, soldered it again lol.
A lot of work done today. I understanded CAN, got it to working, failed it, got it to work again....
Im crooked rn, letme go sleep guyz.

Lapse it is *but im dyin lol*:
https://lapse.hackclub.com/timelapse/tlmj2piRnfcS
(I got one break, 8 to 9hr of recording, i forgot to stop lapse, but after short snack break i forgot to turn it back on. I have 13hrs on my work timer ":skulker:")

Imagesss!










**Total time spent: 12 hours**

# July 11: anode day anode problym

Yeeee!
I soldered another motor driver... And now one is working flawlewsy and other one got problem with can.
I get only few messeges and i drop some, while other one with entirely same hardware works. 
Is there any specialist who knows how to CAN, not CANnot?

But hey! After all i got one can to working and now i somewhat learned it and understand it now!

Lapse:
https://lapse.hackclub.com/timelapse/sVqIrzqbEWA-
(Dinner break, 6.02 to 6.58, i forgot to turn off lapse)

Journal reel:
https://forge.hackclub.com/reels/146

Imagesss!






**Total time spent: 10.3 hours**

# July 12: It is literally bright outside lol

Today was a big day. Kidding. Just a long day lol.
From morning to about 7pm i was trying everything to make CAN work. It was warking flawlessly on one PCB and not on other. In the proces i touched +12v onto +3.3v and broke mcu. Good i have bought 4pieces of this exact mcu from ali like a month ago... right!
WROOOOONG! They were all wrong! I soldered one and for another long fucking work time, without realising was trying to CAN... on like 2AM i realised that this might be beacouse of aliexpress mcu. It didnt even cross my mind, beacuse they looked good!
When trying to initialize interrupts and timers mcu just stopps working... With light code, without anything, just while-loop there were no problemos my friendos....

So ye, after that i just joinked every mcu i had on my driver, soldering, desoldering, soldering, desoldering, soldering... and then! To my suprise! Last one was just working! one from batch of 4. 25% of working mcu. 75% Dead on arrival.
Hellye. So it just worked. What about second driver? I had to take serious decision. Desolder mcu from my other robot, and make it unusable or joinked this robot... Yk what i have done. OFC WE ARE DOIN RISKY WAY!

So after soldering and desoldering and cooking this poor PCB work like another one and a holf an hour (remember, this is ufqfpn-48, so very small pads, not so easy to solder) i got everyhitng to work. 

from 3.30AM to 4AM i was just clearing up code from testing and "trying to fix" leftovers. I will remember this night forever lol.

**BBBIG LESSON FOR EVEYRONE:**
**TRY NO TO BUY IMPORTANT ICs FROM ALIEXPRESS - THEY CAN SCAM YOU**
*resistor, capacitors, and other easy/passive components are okay, but VERY FUCKING IMPORTANT MCU might not be best idea to aliexpress*

Ahh yeee, and i got all line and distance sensors soldered and hooked up!

lapse froze and broke at 12hrs of recording... I realised this after a loooong time lol :skulk:. I started working around 11.30 in the morning and finished about 4.00 at night, with about two half an hour breaks, lets add another half an hour for stuff like eating snacks and times where i lost focus on main goal, etc...
Long lapse:
https://lapse.hackclub.com/timelapse/SSPbA1fPo_17
2AM lapse:
https://lapse.hackclub.com/timelapse/Cs3l5lJ24dIN

Imagesss!






**Total time spent: 15 hours**

# July 13: Last day before going offline for a week!

__ITS FLIPPING WORKS GUYS__

_67676767676767676767676_

(code writing, got to fix some minor soldering issues)
Lapse:
https://lapse.hackclub.com/timelapse/znTl7opDQoub

No images, but reels today!
https://forge.hackclub.com/reels/147
https://forge.hackclub.com/reels/148

__HELLFUCKINGYEAH__

_It is fully autonomus byt the way... And its only 40% power!_

_nvm hers image, AI is mad at me for not having one_

**Total time spent: 1.5 hours**

# July 20: 67

got oled to working ;-;
i got some problems beacuse my library didnt allow 64x32 oled, but after a lot of tinkering and help of unc google and chatgpt i managed to make it work!
Also all of my sensors, but one are working!
Lapse:
https://lapse.hackclub.com/timelapse/UPXGVnVu585F

**Total time spent: 5.5 hours**

# July 22: Hello here

I got full init oled information! Now i know when my robot is talking with lidars, when with motor drivers and when he is ready!
*And when something is borked lol - say what you want but this is SO FUCKIN USEFULL*

Also i had one distance sensor not working, ya'll remember? I got it to work.
At the price of burning MCU. This time it is last one. 
Unfortunetaly in whole process i ripped like 3 pads, so i had to wire them by hand with .1mm copper wire :skulkerer:

And ye. As for today i have everything __BUT__ can :cry:
I dont know why. it worked before. But now i CANNOT ?-?!

Lapse:
https://lapse.hackclub.com/timelapse/jAqGxBFecOSW




**Total time spent: 7.4 hours**

# July 22: LOOKS SOOO FLIPPIN DOPE!

YAY! I got it from not working to working again! Replacing mainboard connector with new ones was the thing to do!
Now my drivers work!

Also i made ui and all of the nice cool stuff, like undervoltage protection!
My battery voltage redouts wasnt working so i just joinked it, removed protection diode and it is working like a bliss now looool

And yup, i had to solder some pads wiht 0.04mm (human hair is freakin 0.1mm bytheway) copper wire, beacuse i ripped like 6 od 7 padssss

It is miracle. I didnt believe it would work anymore.
More coding more coding, i also got to write whole START MODULE operations, like wait for signal, read signal, when signal set start_flag to TRUE, etcetra.

Aaalsoo some calculations. I have exactly 200MS to stop before going extinc!

Lapse:
https://lapse.hackclub.com/timelapse/-6MXYkGq6m6p






**Total time spent: 6 hours**

# August 04: Finnaly got my hands on start remote!

Comeback after long breakkkk! HELLYE!
Yesterday i borrowed start remote from out robotics club!
Without it i could propelly test IR receiver functionality. I had som shienienigans problems, but after long debuging and talking with chat, changing timer settings and SIRC/CR5 timeframes worked.
After that i changed a lil bit my rims, so i could cast them again. Ones i made before arent bad, but they are a little bit off center, which makes be angryyyyyy

so yeee! Coming after that i programed starting sequence, as rulebook require.
Remember guys to not use any HAL_Delay or SLEEP functions, if you are working mainly on interrupts, beacuse they will break your cede lol.
Literally. They will render it unusableee.. Why? Beacuse MCU tries to do his job at working out all of your functions event and interrupts, when YOINK! NAH MEN - you gotta wait for SLEEP(67) miliseconds, lol
And everything breaks!

Lapse:
https://lapse.hackclub.com/timelapse/j1nPhS0W8PA5




**Total time spent: 4.9 hours**

# August 05: Last day of work before competition...

Last day...
Today i got rims which i designed yesterday, from my brother and casted them. Ofc they didnt hardened yet, but they will be ready for championship!

I have wrote attack sequences and all of that. I wanted to add one attack mode, in which robot just go into circles on the edge of the dohyo, to suprise opponent and gain high ground...
But after all i suck at line following, so no-good. I lost it all lol. No line following for me :)
Problem may be that i for that i can only use 2 sensor, one on the front and one on the back, which may be not enought for smoooth line following experience.

Maybe i will rock it at the beggining of the championship, if i will have some time for minor fixes and additions like that!
So guys... Wish me luck at the "RoboRAVE Word Championship 2025"!

*ah yes, also i added proper photos to readme! Im more than these prototype-shit photos lol*

Lapse:
https://lapse.hackclub.com/timelapse/Y0BkItvrs7Am


**Total time spent: 3 hours**

# August 10: Night before competition

Today i made all of the check before competition.
I didnt know it before, byt dohyo at RoboRave have reversed color -> i had to reprogram line sensors.
Alsooo they sent everyone an email at 2AM, that they changed rules and starting sequence...
I HAD TO FUCKING REPROGRAM THIS SEQUENCE AT NIGHT BROSSS.

Also i spent like 4hr at sharpeping my front plow. I hope it will be better than these guys sharp knifes!


**Total time spent: 6 hours**

# August 11: First competition day!

Im fucking furious and not in the same time lol.
Today i spent full day testing and fixing robot. I was supposed to have more than half of planned fights, but organisation was so cooked, that i didnt had even one fight lol.

I had so much problem w ith line sensors. They were cooked. After a lot of testing i found out, that when line sensors is far from ground plane it dont sense any received ground, same as on black - while sensors is over white it sense all of the emited light. Main poroblem is that i have short robot and My front constantly go up, beacuse of my freakin powerfull motors!

Main idea to fix it was to add accelerataion curve. Instead of going FULL POWER FOR MOTORS i changed into give them little bit more than before, until hits 100% PWM. Not they work okayish!

After that i fixed some attack code, got all of the values for velocities, max speed, distances etcetra.
And that was it for a full day!

In the night i tried to make line follower mode work at faster speeds but with none success... The main problem is that i have not enough line sensors, so it is just borked. At the beggining i tried to do PID tuning, but pid with one digital sensor isnt really pid LOL. It is just a D i think.

So i sticked with normal ELSEIF statements and i managed to somewhat use Front as well as Back line sensor. 
After all it was too borked to use it safely in a competition, so i didnt use it at all.


**Total time spent: 12.3 hours**

# August 12: Competition date!

Competition dayyy!

I got some fights! As yesterday we arrived there like 3hrs before start of the competition, so about 8AM and stayed there till 6PM.
Thanks to that i got pleeeeenty of time for actual testing. Thanks to my friend (WHO ACTUALLY GOT 1ST PLACE AT WHOLE COMPETITION!!! CONGRATS MANIEK!) i discovered that my distance sensors arent working propelly.

I had to lessen filtration and add some IFs. I changed AMP treschold little bit down and added statment, when distance is lower than about 10CM, then i dont care about AMP... AMP is strenght of received IR signal. This is why these sensors dont costs 5bucks lol. They work like a charm <3

With some robot to test against I perfected values to attack and curve attack.

Reels from fight!:
https://forge.hackclub.com/reels/170
https://forge.hackclub.com/reels/171

*Guys, i pushed out FUCKIN 3KG ROBOT while my weight was 850G only LOL*

After all of the fights i reached my conclusion that:
    - My plow wasnt as hard as i wanted, and my opponets plows were sometimes sharper
    - I want a little bit more distance sensors in future robots
    - Overall it is a great robot!

*Also quick readme update with certificate!*


**Total time spent: 6.4 hours**

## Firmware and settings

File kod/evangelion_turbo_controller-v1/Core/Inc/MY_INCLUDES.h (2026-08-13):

/*
 * MY_INCLUDES.h
 *
 *  Created on: Jun 26, 2026
 *      Author: szymo
 */

#ifndef INC_MY_INCLUDES_H_
#define INC_MY_INCLUDES_H_


//==================================================== SENSORS
#define MIN_AMP_TRESCHOLD 						50
#define MIN_LIDAR_AMP_DIST						20
#define MIN_LIDAR_AMP_DIST_AMP					500
#define MAX_RETRIES_LIDARS_INIT 				7
#define LIDARS_INIT_UART_TIMEOUT 				150
#define LIDARS_FILTERING_ARRAY_SIZE_FRONT		7
#define LIDARS_FILTERING_ARRAY_SIZE_BACK		9
#define MAX_LIDAR_DISTANCE 						60 //60
#define LIDAR_DIST_FOR_LINE_FOLLOWER_ATCK_PLS_BE_BACK	30
#define MIN_LIDAR_DISTANCE 						20 //20
#define INTRO_MIN_DISTANCE_FOR_LAST_SEEN		5
#define WHITE_LINE_TRESCHOLD_FOR_BLACK_DOHYO	3700 //white is less
#define BLACK_LINE_TRESCHOLD_FOR_WHITE_DOHYO	3700 //black is more

#define LINE_COMEBACK_TIME						300
#define LINE_COMEBACK_VELOCITY					30


//==================================================== MOTR DRIVERs
#define MAX_RETRIES_DRIVER_INIT 			5
#define DRIVER_INIT_CAN_TIMEOUT 			100
#define MAX_FET_TEMP 						60
#define MAX_MOTOR_CURRENT_SHORT 			16
#define MAX_MOTOR_CURRENT_LONG 				8
#define MAX_MOTOR_ACCELERATION				0	//from 0, which is instant, to 250ms which is long
#define SWITCH_MOTORS 						FALSE
#define REVERSE_RIGHT_MOTOR 				FALSE
#define REVERSE_LEFT_MOTOR 					FALSE
#define LEFT_MOTOR_VELOCITY_MULTIPLIER 		1
#define RIGHT_MOTOR_VELOCITY_MULTIPLIER 	0.94
#define MAX_MOTOR_ACCELERATION_NOT_DECELERATION_BY_CONTROLLER	100


//==================================================== ATTACK MODES SETTINGS AND TASK QUESTIONS
#define START_WAITING_TIME 					3000 //3000
#define START_WAITING_TIME_HEADROOM			100

#define GO_TO_LINE_TASK_SPEED 				35
#define AFTER_TASK_ALIGMENT_SPEED 			30
#define AFTER_TASK_ROTATION_TIME			50
#define STARTING_ROAM_TIME_QUCKIE			10 //3 cykle xD
#define STARTING_ROAM_TIME_CHILL			175

//============================================= STRAIGHT ATTACK
#define SEARCH_STRAIGHT_ATTACK_SPEED		30
#define ATTACK_STRAIGHT_ATTACK_SPEED		80


//============================================= CURVE ATTACK
#define CURVE_ATTACK_ONE_SEE_ATTACK_SPEED_FASTER 60
#define CURVE_ATTACK_SEARCH_SPEED_FASTER 50
#define CURVE_ATTACK_SEARCH_SPEED_SLOWER 25


//============================================= FOLLOW LINER and ATTACKER
#define FOLLOW_LINER_FASTER 40
#define FOLLOW_LINER_SLOWER 30
#define MAX_MOTOR_ACCELERATION_FOR_LINE_FOLLOWING 20


//==================================================== BUZZER
#define FREQ_STARTING 			300
#define FREQ_STEP_INIT			75


//==================================================== SETTINGS
#define DISABLE_OLED								FALSE
#define DEFAULT_SETTING_BATTERY_CELL_NO				3
#define DEFAULT_SETTING_DONT_USE_MOTORS				FALSE
#define DEFAULT_SETTING_ALWAYS_IN_BATTLE			FALSE
#define DEFAULT_SETTING_IGNORE_START_MODULE			FALSE
#define DEFAULT_SETTING_LINE_SENSORS_ALWAYS_IN		FALSE
#define DEFAULT_SETTING_ENABLE_BUZZER				FALSE
#define DEFAULT_SETTING_DONT_INITIALIZE_LIDARS		FALSE
#define DEFAULT_SETTING_ALWAYS_SHOW_OLED			TRUE
#define DEFAULT_ATTACK_MODE_ID						0
#define DEFAULT_RING_COLOR_IS_WHITE					TRUE
#define SPECIAL_STARTING_SEQUENCE					TRUE


//================================================================================================INIT ERRORS
//================================================================================================INIT ERRORS
//================================================================================================INIT ERRORS
#define START_SIGNAL_AT_STARTUP 1

#define TIM1_INIT_ERR 2
#define TIM2_INIT_ERR 3
#define TIM3_INIT_ERR 4
#define TIM4_INIT_ERR 5

#define ADC_INIT_ERR 6

#define BATTLE_TIM_INIT_ERR 10
#define WATCHDOG_TIM_INIT_ERR 11
#define OLED_TIM_INIT_ERR 12
#define LIDARS_INIT_ERR 13
#define DRV_INIT_ERROR 16



#define START_MOD_UART_CONNECTION_COOKED 24


//===================================
#define START_DELAY_IN_USE 200

//===================================BAD_ERRORS >200, no HALT of mcu
#define OLED_INIT_ERR 201
#define LOW_BATTERY_VOLTAGE 200

//==================================================== ERROR FLAGS
//<200 init error flags
//==200 start delay
//>200 error, veery bad error
//in separate file


#endif /* INC_MY_INCLUDES_H_ */

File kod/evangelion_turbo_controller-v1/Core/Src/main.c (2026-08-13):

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
/* Includes ------------------------------------------------------------------*/
#include "main.h"

/* USER CODE BEGIN Includes */
#include "stdlib.h"
#include "MY_INCLUDES.h"

#include "fonts.h"
#include "ssd1306.h"
/* USER CODE END Includes */

/* USER CODE BEGIN PD */
#define DMA_HANDLE_UART1 &handle_GPDMA1_Channel1
#define DMA_HANDLE_UART2 &handle_GPDMA1_Channel2
#define DMA_HANDLE_UART4 &handle_GPDMA1_Channel4
#define DMA_HANDLE_UART5 &handle_GPDMA1_Channel5

#define CAN_ID_CTRL  60
#define CAN_ID_DRV0  67
#define CAN_ID_DRV1  69


//==================================================== WORKING SETUP
#define MAIN_FREQ 1000
#define SIDE_FREQ 100
#define OLED_FREQ 25
#define true 1
#define TRUE 1
#define false 0
#define FALSE 0
#define LEFT 0
#define RIGHT 1


//============etc
#define ABS(x) ((x) < 0 ? -(x) : (x))


//option IDs
#define OPTION_ID_BATTERY 1
#define OPTION_ID_START_MOD 2
#define OPTION_ID_LUNA_DIST 3
#define OPTION_ID_LUNA_AMP 4
#define OPTION_ID_LINES 6
#define OPTION_ID_ACCEL 7
#define OPTION_ID_GYRO 8
#define OPTION_ID_IMU_PEAK 9
#define OPTION_ID_SET_MOTS 10
#define OPTION_ID_DEBUG 11
#define OPTION_ID_ATTACK_MODE 12

//==================================================== BATTERY
#define BATTERY_VOLTAGE_COMPENSATION 	1
#define MIN_BATTERY_VOLTAGE_PER_CELL 	3.45
#define Reference_Voltage				3.311		// V
#define Voltage_Resistor_Top 			91.0		// kOhm
#define Voltage_Resistor_Bottom  		10.0		// kOhm
#define ADC_MAX_VALUE					4096


//==================================================== OLED
#define _ssd1306_SetCursor(x, y) ssd1306_SetCursor(y, x)
#define BIG 1
#define SMALL 0

#define _ARR_UP '('
#define _ARR_DOWN '@'
#define _CHECKBOX_EMPTY '^'
#define _CHECKBOX_CHECKED '$'
#define _CHECKBOX_EMPTY_BIG ')'
#define _CHECKBOX_CHECKED_BIG '\''
#define _CANCEL '}'
#define _APPLY '{'

//=============================================================================================================
//=============================================================================================================			START MOD CODE
//=============================================================================================================
#define RISING 		1
#define FALLING		2
#define TIMEOUT		3

#define RC5				1
#define SIRC			2
#define UNKNOWN			0
#define SAVED_STATUS 	5

#define RC5_Short   889      // 889 us
#define RC5_Long    1778     // 1778 us
#define SIRC_Short  600+50      // 600 us
#define SIRC_Long   1200+50     // 1200 us
#define Margin      300

// Module Status
#define STARTUP		1
#define	PPROGRAMMED	2
#define	READY		3
#define	RC5_START	4
#define SIRC_START	5
#define	STOP		6

// Led Commands
#define ON			2
#define OFF			3
#define BLINK_SLOW	4
#define BLINK_FAST	5
#define TICK		6


/* USER CODE END PD */

/* USER CODE BEGIN PM */
typedef struct {
	uint8_t DONT_USE_MOTORS;
	uint8_t ALWAYS_IN_BATTLE;
	uint8_t IGNORE_START_MODULE;
	uint8_t LINE_SENSORS_ALWAYS_IN;
	uint8_t IGNORE_ACCEL;
	uint8_t DONT_INITIALIZE_LIDARS;
} Settings_t;

typedef enum {
	IN,
	OUT
} LineState_t;

typedef enum {
	STRAIGHT,
	CURVE,
	FOLLOW_LINER,
	FOLLOW_ATTACKER,
	COUNT,
} RobotAttackMode_t;

typedef enum
{
	IDLE,
	BEFORE_ATTACK_WAIT,
	BEFORE_ATTACK_TASK,
	AFTER_TASK_RAM_QUCKIE,
	AFTER_TASK_RAM_CHILL,
	ATTACK,
} RobotState_t;

typedef enum {
	_NOTHING,
	_UP,
	_DOWN,
	_LEFT,
	_RIGHT,
	_CENTER,
	_BUTTON_REBOUNCE,
} JoystickMode_t;

typedef struct {
	LineState_t Line;
	uint16_t RawLineA;
	uint16_t RawLineB;
    uint16_t Distance;
    uint16_t LidarAmp;
    uint16_t LidarTemp;
} SensorData_t;

typedef struct {
	uint8_t Switch1;
	uint8_t Switch2;
	uint8_t Switch3;
	JoystickMode_t Joystick;
	uint8_t MenuOption;
} Interface_t;

typedef struct
{
	int16_t x;
	int16_t y;
	int16_t z;
	int16_t peak;
} Vector_t;

typedef struct {
	uint8_t inBattle;
	RobotAttackMode_t AttackMode;
	uint16_t Voltage;
	uint16_t CellVoltage;
	RobotState_t State;
	Interface_t Interface;
	uint8_t DriverTemp;
	uint16_t StartDelayTimer;
} RobotData_t;


typedef struct {
	uint8_t CurrentAddres;
	uint8_t Started;
	uint8_t StartedViaInterface;
	uint8_t StartedViaSwitch;
	uint16_t Delay;
	uint16_t VolatileDelayTimer;
} StartModData_t;


typedef struct
{
	int8_t L;
	int8_t R;
} Speed_t;

typedef struct
{
	uint8_t L;
	uint8_t R;
} Speed_directional_t;

typedef struct
{
	Speed_t Requested;
	Speed_t Set;
	Speed_directional_t CAN;
} MotorSpeed_t;

typedef struct {
    const char *name;
    uint8_t id;
} MenuOption_t;

/* USER CODE END PM */

ADC_HandleTypeDef hadc1;
DMA_NodeTypeDef Node_GPDMA2_Channel0;
DMA_QListTypeDef List_GPDMA2_Channel0;
DMA_HandleTypeDef handle_GPDMA2_Channel0;

FDCAN_HandleTypeDef hfdcan1;

I2C_HandleTypeDef hi2c1;
I2C_HandleTypeDef hi2c3;
DMA_HandleTypeDef handle_GPDMA2_Channel1;

TIM_HandleTypeDef htim3;
TIM_HandleTypeDef htim6;
TIM_HandleTypeDef htim7;
TIM_HandleTypeDef htim12;
TIM_HandleTypeDef htim13;
TIM_HandleTypeDef htim14;
TIM_HandleTypeDef htim15;
TIM_HandleTypeDef htim16;
TIM_HandleTypeDef htim17;

UART_HandleTypeDef huart4;
UART_HandleTypeDef huart5;
UART_HandleTypeDef huart1;
UART_HandleTypeDef huart2;
DMA_HandleTypeDef handle_GPDMA1_Channel4;
DMA_HandleTypeDef handle_GPDMA1_Channel5;
DMA_HandleTypeDef handle_GPDMA1_Channel1;
DMA_HandleTypeDef handle_GPDMA1_Channel2;

/* USER CODE BEGIN PV */
//CAN
FDCAN_RxHeaderTypeDef 		CAN_RX_Header; 		//CAN Bus Transmit Header
FDCAN_TxHeaderTypeDef 		CAN_TX_Header; 		//CAN Bus Receive Header
uint8_t                     CAN_TX[8];
uint8_t                     CAN_RX[8];
FDCAN_FilterTypeDef 		CAN_Filter;

volatile int32_t dupa=0;
volatile int32_t dupa2=0;
uint16_t actual_init_freq=FREQ_STARTING;
int16_t ERROR_FLAG=0;

//sensors
uint8_t  UART1_RX[9];
uint8_t  UART2_RX[9];
uint8_t  UART4_RX[9];
uint8_t  UART5_RX[9];
uint8_t  UART_TX[9];

SensorData_t FrontLeft={0};
SensorData_t FrontRight={0};
SensorData_t BackLeft={0};
SensorData_t BackRight={0};
RobotData_t Eva={0};
MotorSpeed_t Motors={0};
StartModData_t StartMod={0};
Settings_t Settings={0};

uint8_t lastSeen = LEFT;
uint8_t before_attack_rotation_direction = LEFT;

volatile uint16_t ADC_BUFFER[9];
float BATTERY_CONSTANT;


//performance!
static uint32_t last_total = 0;
static uint32_t last_idle = 0;
volatile uint32_t cpu_idle_cycles = 0;
volatile uint32_t cpu_load_permille = 0;
volatile uint8_t MCU_LOAD = 0;
volatile uint8_t MCU_LOAD_MAX = 0;

//============================		START MOD CODE
uint8_t Module_State = STARTUP;
static uint8_t Dohyo_ID=0;
uint8_t MAX_ACCELERATION=0;
/* USER CODE END PV */

void SystemClock_Config(void);
static void MX_GPIO_Init(void);
static void MX_GPDMA1_Init(void);
static void MX_GPDMA2_Init(void);
static void MX_ADC1_Init(void);
static void MX_FDCAN1_Init(void);
static void MX_I2C3_Init(void);
static void MX_TIM3_Init(void);
static void MX_UART4_Init(void);
static void MX_UART5_Init(void);
static void MX_USART2_UART_Init(void);
static void MX_USART1_UART_Init(void);
static void MX_TIM16_Init(void);
static void MX_TIM17_Init(void);
static void MX_I2C1_Init(void);
static void MX_TIM14_Init(void);
static void MX_TIM12_Init(void);
static void MX_TIM13_Init(void);
static void MX_TIM15_Init(void);
static void MX_TIM6_Init(void);
static void MX_TIM7_Init(void);
/* USER CODE BEGIN PFP */
static void LIDARS_INIT(UART_HandleTypeDef *huart, DMA_HandleTypeDef *hdma, uint8_t *RX);
static void PLAY_FREQ(uint16_t f_hz);
static void COOKED(uint8_t error_code);
static void SORT(uint16_t *array, uint8_t length);
static void GET_LINE_SENSORS(void);
static void GET_START_MOD(void);
static void STRAIGHT_ATTACK(void);
static void CURVE_ATTACK(void);
static void FOLLOWLINER_ATTACK(void);
static void FOLLOW_ATTACKER_ATTACK(void);
static void WATCHDOG(void);
static void GET_LAST_SEEN_ROTATIONE(void);
static void TASK_BEFORE_ATTACK(void);
static void SET_MOTORS(int8_t l, int8_t r);
static void SET_RAW_MOTORS(int8_t l, int8_t r);
static void _ssd1306_WriteInTheMiddle(char *text, uint8_t y, uint8_t font);
static void _ssd1306_WriteString(char* str, uint8_t font);
static void MOTOR_DRIVER_INIT(uint8_t DRV_SELF_ADDRESS);
static uint8_t ARE_ELEMENTS_EQUAL(const uint8_t *a, const uint8_t *b, uint8_t n);
static int8_t Acceleration_Compensation_R(int8_t Duty);
static int8_t Acceleration_Compensation_L(int8_t Duty);
static void OLED(void);
static inline void DWT_Init(void);

//============================		START MOD CODE
static void Interrupt10Hz(void);
static void Interrupt(uint8_t Edge);
static void Received_RC5_Frame(uint8_t Addres, uint8_t Command);
static void Received_SIRC_Frame(uint8_t Addres, uint8_t Command);
static uint8_t LED_GREEN_Control(uint8_t Command, uint8_t Data);
static uint8_t LED_RED_Control(uint8_t Command, uint8_t Data);
static uint8_t LED_BLUE_Control(uint8_t Command, uint8_t Data);
/* USER CODE END PFP */

/**
  * @brief  The application entry point.
  * @retval int
  */
int main(void)
{

  /* USER CODE BEGIN 1 */
    Eva.AttackMode = DEFAULT_ATTACK_MODE_ID;
    MAX_ACCELERATION = MAX_MOTOR_ACCELERATION_NOT_DECELERATION_BY_CONTROLLER;

  /* USER CODE END 1 */

  /* MCU Configuration--------------------------------------------------------*/

  /* Reset of all peripherals, Initializes the Flash interface and the Systick. */
  HAL_Init();

  /* USER CODE BEGIN Init */
  HAL_Delay(100);
  /* USER CODE END Init */

  /* Configure the system clock */
  SystemClock_Config();

  /* Initialize all configured peripherals */
  MX_GPIO_Init();
  MX_GPDMA1_Init();
  MX_GPDMA2_Init();
  MX_ADC1_Init();
  MX_FDCAN1_Init();
  MX_I2C3_Init();
  MX_TIM3_Init();
  MX_UART4_Init();
  MX_UART5_Init();
  MX_USART2_UART_Init();
  MX_USART1_UART_Init();
  MX_TIM16_Init();
  MX_TIM17_Init();
  MX_I2C1_Init();
  MX_TIM14_Init();
  MX_TIM12_Init();
  MX_TIM13_Init();
  MX_TIM15_Init();
  MX_TIM6_Init();
  MX_TIM7_Init();
  /* USER CODE BEGIN 2 */

  static uint8_t init_text_height = 0;
  static uint8_t init_secondary_text_height = 20;
  static uint8_t init_everywhere_delay = 50;

	//INTIT
	actual_init_freq = actual_init_freq + FREQ_STEP_INIT;
	PLAY_FREQ(actual_init_freq);
	if(ssd1306_Init()==0)
		Error_Handler();
	ssd1306_Clear();
	ssd1306_SetColor(White);
	ssd1306_Fill();
	ssd1306_UpdateScreen();
	HAL_Delay(init_everywhere_delay);


	//CAN FILTERS
	ssd1306_Clear();
	_ssd1306_WriteInTheMiddle("CAN", init_text_height, BIG);
	_ssd1306_WriteInTheMiddle("initialize", init_secondary_text_height, SMALL);
	ssd1306_UpdateScreen();
	HAL_Delay(init_everywhere_delay);
	CAN_Filter.IdType = FDCAN_STANDARD_ID;
	CAN_Filter.FilterIndex = 0;
	CAN_Filter.FilterType = FDCAN_FILTER_DISABLE;
	CAN_Filter.FilterConfig = FDCAN_FILTER_TO_RXFIFO0;
	CAN_Filter.FilterID1 = 0;
	CAN_Filter.FilterID2 = 0;
	HAL_FDCAN_ConfigFilter(&hfdcan1, &CAN_Filter);

	//CAN SETTINGS
	CAN_TX_Header.Identifier = CAN_ID_CTRL;
	CAN_TX_Header.IdType = FDCAN_STANDARD_ID;
	CAN_TX_Header.TxFrameType = FDCAN_DATA_FRAME;
	CAN_TX_Header.DataLength = FDCAN_DLC_BYTES_8;
	CAN_TX_Header.ErrorStateIndicator = FDCAN_ESI_ACTIVE;
	CAN_TX_Header.TxEventFifoControl = FDCAN_NO_TX_EVENTS;
	CAN_TX_Header.MessageMarker = 0;
	CAN_TX_Header.FDFormat = FDCAN_CLASSIC_CAN;
	CAN_TX_Header.BitRateSwitch = FDCAN_BRS_OFF;

	BATTERY_CONSTANT = ((Voltage_Resistor_Top + Voltage_Resistor_Bottom) / Voltage_Resistor_Bottom) * Reference_Voltage / 4096 * 100;

	Settings.ALWAYS_IN_BATTLE = DEFAULT_SETTING_ALWAYS_IN_BATTLE;
	Settings.DONT_INITIALIZE_LIDARS = DEFAULT_SETTING_DONT_INITIALIZE_LIDARS;
	Settings.DONT_USE_MOTORS = DEFAULT_SETTING_DONT_USE_MOTORS;
	Settings.IGNORE_START_MODULE = DEFAULT_SETTING_IGNORE_START_MODULE;

	lastSeen = LEFT;
	Eva.inBattle = FALSE;
	Eva.State = IDLE;
	Eva.AttackMode = DEFAULT_ATTACK_MODE_ID;
	Eva.StartDelayTimer = 0;


	//GPIO LED MISC
	actual_init_freq = actual_init_freq + FREQ_STEP_INIT;
	PLAY_FREQ(actual_init_freq);
	HAL_GPIO_WritePin(LED_RED_GPIO_Port, LED_RED_Pin, 0);
	HAL_GPIO_WritePin(LED_BLUE_GPIO_Port, LED_BLUE_Pin, 0);
	HAL_GPIO_WritePin(LED_GREEN_GPIO_Port, LED_GREEN_Pin, 1);
	HAL_GPIO_WritePin(CAN_EN_GPIO_Port, CAN_EN_Pin, 1);
	HAL_Delay(init_everywhere_delay);



	//start mode setup
	//============================		START MOD CODE
    Module_State = STARTUP;
	ssd1306_Clear();
	_ssd1306_WriteInTheMiddle("START", init_text_height, BIG);
	_ssd1306_WriteInTheMiddle("MODULE", init_secondary_text_height, SMALL);
	ssd1306_UpdateScreen();
	HAL_Delay(init_everywhere_delay);
	//  Signal Power UP
	HAL_GPIO_WritePin(LED_RED_GPIO_Port, LED_RED_Pin, GPIO_PIN_SET);
	HAL_Delay(125);
	HAL_GPIO_WritePin(LED_RED_GPIO_Port, LED_RED_Pin, GPIO_PIN_RESET);
	HAL_GPIO_WritePin(LED_BLUE_GPIO_Port, LED_BLUE_Pin, GPIO_PIN_SET);
	HAL_Delay(125);
	HAL_GPIO_WritePin(LED_BLUE_GPIO_Port, LED_BLUE_Pin, GPIO_PIN_RESET);
	HAL_GPIO_WritePin(LED_GREEN_GPIO_Port, LED_GREEN_Pin, GPIO_PIN_SET);
	HAL_Delay(250);
	HAL_GPIO_WritePin(LED_GREEN_GPIO_Port, LED_GREEN_Pin, GPIO_PIN_RESET);

	//LUNAS
	ssd1306_Clear();
	_ssd1306_WriteInTheMiddle("LIDARS", init_text_height, BIG);
	ssd1306_UpdateScreen();
	HAL_Delay(init_everywhere_delay);
	actual_init_freq = actual_init_freq + FREQ_STEP_INIT;
	PLAY_FREQ(actual_init_freq);
	if(Settings.DONT_INITIALIZE_LIDARS == FALSE)
	{
		ssd1306_Clear();
		_ssd1306_WriteInTheMiddle("LIDARS", init_text_height, BIG);
		_ssd1306_WriteInTheMiddle("front right", init_secondary_text_height, SMALL);
		ssd1306_UpdateScreen();
		LIDARS_INIT(&huart2, DMA_HANDLE_UART2, UART2_RX);

		ssd1306_Clear();
		_ssd1306_WriteInTheMiddle("LIDARS", init_text_height, BIG);
		_ssd1306_WriteInTheMiddle("front left", init_secondary_text_height, SMALL);
		ssd1306_UpdateScreen();
		LIDARS_INIT(&huart5, DMA_HANDLE_UART5, UART5_RX);

		ssd1306_Clear();
		_ssd1306_WriteInTheMiddle("LIDARS", init_text_height, BIG);
		_ssd1306_WriteInTheMiddle("back left", init_secondary_text_height, SMALL);
		ssd1306_UpdateScreen();
		LIDARS_INIT(&huart1, DMA_HANDLE_UART1, UART1_RX);

		ssd1306_Clear();
		_ssd1306_WriteInTheMiddle("LIDAR", init_text_height, BIG);
		_ssd1306_WriteInTheMiddle("back right", init_secondary_text_height, SMALL);
		ssd1306_UpdateScreen();
		LIDARS_INIT(&huart4, DMA_HANDLE_UART4, UART4_RX);
		/*
		uart1 = back left
		uart2 = front right
		uart4 = back right
		uart5 = front left
		*/
	}



	//ADC
	ssd1306_Clear();
	_ssd1306_WriteInTheMiddle("ADCs", init_text_height, BIG);
	ssd1306_UpdateScreen();
	HAL_Delay(init_everywhere_delay);
	actual_init_freq = actual_init_freq + FREQ_STEP_INIT;
	PLAY_FREQ(actual_init_freq);
	if (HAL_ADCEx_Calibration_Start(&hadc1, ADC_SINGLE_ENDED) != HAL_OK)
	  COOKED(ADC_INIT_ERR);
	HAL_Delay(50);

	if (HAL_ADC_Start_DMA(&hadc1, (uint32_t*)ADC_BUFFER, 9) != HAL_OK)
	  COOKED(ADC_INIT_ERR);

	//CAN
	ssd1306_Clear();
	_ssd1306_WriteInTheMiddle("DRVs", init_text_height, BIG);
	_ssd1306_WriteInTheMiddle("CAN start", init_secondary_text_height, SMALL);
	ssd1306_UpdateScreen();
	HAL_Delay(init_everywhere_delay);
	actual_init_freq = actual_init_freq + FREQ_STEP_INIT;
	PLAY_FREQ(actual_init_freq);
	if (HAL_FDCAN_Start(&hfdcan1) != HAL_OK)
		Error_Handler();
	HAL_FDCAN_ActivateNotification(&hfdcan1, FDCAN_IT_RX_FIFO0_NEW_MESSAGE, 0);
	HAL_FDCAN_AddMessageToTxFifoQ(&hfdcan1, &CAN_TX_Header, CAN_TX);

	//DRV1
	ssd1306_Clear();
	_ssd1306_WriteInTheMiddle("DRVs", init_text_height, BIG);
	_ssd1306_WriteInTheMiddle("DRV 0 init", init_secondary_text_height, SMALL);
	ssd1306_UpdateScreen();
	HAL_Delay(init_everywhere_delay);
	MOTOR_DRIVER_INIT(CAN_ID_DRV0);

	//DRV2
	ssd1306_Clear();
	_ssd1306_WriteInTheMiddle("DRVs", init_text_height, BIG);
	_ssd1306_WriteInTheMiddle("DRV 1 init", init_secondary_text_height, SMALL);
	ssd1306_UpdateScreen();
	HAL_Delay(init_everywhere_delay);
	MOTOR_DRIVER_INIT(CAN_ID_DRV1);

	//Performance
	ssd1306_Clear();
	_ssd1306_WriteInTheMiddle("MCU", init_text_height, BIG);
	_ssd1306_WriteInTheMiddle("performance", init_secondary_text_height, SMALL);
	ssd1306_UpdateScreen();
	HAL_Delay(init_everywhere_delay);
	actual_init_freq = actual_init_freq + FREQ_STEP_INIT;
	PLAY_FREQ(actual_init_freq);
	DWT_Init();

	//Interrupts
	ssd1306_Clear();
	_ssd1306_WriteInTheMiddle("ITs", init_text_height, BIG);
	_ssd1306_WriteInTheMiddle("start", init_secondary_text_height, SMALL);
	ssd1306_UpdateScreen();
	HAL_Delay(init_everywhere_delay);
	actual_init_freq = actual_init_freq + FREQ_STEP_INIT;
	PLAY_FREQ(actual_init_freq);
	HAL_TIM_Base_Start_IT(&htim12); //10Hz start mod
	HAL_TIM_Base_Start_IT(&htim13); //1Khz start mod
	HAL_TIM_Base_Start_IT(&htim14); //25Hz oled
	HAL_TIM_Base_Start_IT(&htim16); //1000Hz
	HAL_TIM_Base_Start_IT(&htim17); //100Hz
	HAL_TIM_Base_Start_IT(&htim15); // START_MOD
	HAL_TIM_Base_Start(&htim6);
	HAL_TIM_Base_Start(&htim7);

	HAL_GPIO_WritePin(LED_RED_GPIO_Port, LED_RED_Pin, 0);
	HAL_GPIO_WritePin(LED_BLUE_GPIO_Port, LED_BLUE_Pin, 0);
	HAL_GPIO_WritePin(LED_GREEN_GPIO_Port, LED_GREEN_Pin, 0);
	PLAY_FREQ(0);
	ssd1306_Clear();
	_ssd1306_WriteInTheMiddle("TURBO", 2, SMALL);
	_ssd1306_WriteInTheMiddle("EVA++", 10, BIG);
	ssd1306_UpdateScreen();


  /* USER CODE END 2 */

  /* Infinite loop */
  /* USER CODE BEGIN WHILE */
  while (1)
  {
	uint32_t start = DWT->CYCCNT;
	__WFI();
	cpu_idle_cycles += (DWT->CYCCNT - start);
	CAN_TX_Header.DataLength = FDCAN_DLC_BYTES_4;
    /* USER CODE END WHILE */

    /* USER CODE BEGIN 3 */
  }
  /* USER CODE END 3 */
}

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
/* USER CODE BEGIN 4 */
void HAL_TIM_PeriodElapsedCallback(TIM_HandleTypeDef *htim)
{
	//======================================== Start mod code
	if (htim->Instance == TIM12)
	{
		Interrupt10Hz();
	}
	if (htim->Instance == TIM15)
	{
		Interrupt(TIMEOUT);
	}

	if(htim->Instance == TIM16) //1000Hz battlee
	{
	  GET_LINE_SENSORS();
	  GET_LAST_SEEN_ROTATIONE();
	  GET_START_MOD();
	  if(Eva.State == IDLE)
	  {
		  Eva.StartDelayTimer=0;
	  }
	  else if(Eva.State == ATTACK)
	  {
		  if(Eva.AttackMode == STRAIGHT)
		  {
			  STRAIGHT_ATTACK();
		  }
		  else if(Eva.AttackMode == CURVE)
		  {
			  CURVE_ATTACK();
		  }
		  else if(Eva.AttackMode == FOLLOW_LINER)
		  {
			  FOLLOWLINER_ATTACK();
		  }
		  else if(Eva.AttackMode == FOLLOW_ATTACKER)
		  {
			  FOLLOW_ATTACKER_ATTACK();
		  }
		  else
		  {
			  STRAIGHT_ATTACK();
		  }
	  }
	  else
	  {
		  TASK_BEFORE_ATTACK();
	  }

	}

	if(htim->Instance == TIM17) //100hz everything else
	{
	   WATCHDOG();

	   //LOAD
		uint32_t total = DWT->CYCCNT;
		uint32_t total_diff = total - last_total;
		uint32_t idle_diff  = cpu_idle_cycles - last_idle;

		last_total = total;
		last_idle = cpu_idle_cycles;

		if (total_diff > 0)
			cpu_load_permille = (1000U * (total_diff - idle_diff)) / total_diff;
		else
			cpu_load_permille = 0;

		MCU_LOAD = cpu_load_permille / 10;

		if(MCU_LOAD > MCU_LOAD_MAX)
			MCU_LOAD_MAX = MCU_LOAD;
	}

	if(htim->Instance == TIM14)
	{
		OLED();
	}
}


void STRAIGHT_ATTACK()
{

	static uint16_t ComeBackLinerTimer=UINT16_MAX;
	static uint16_t GoForwardLineAttention=UINT16_MAX;
	static uint16_t BackLineOutGoDirection=LEFT;


	if(ComeBackLinerTimer < LINE_COMEBACK_TIME)
	{
		ComeBackLinerTimer++;
		SET_RAW_MOTORS(-LINE_COMEBACK_VELOCITY,-LINE_COMEBACK_VELOCITY);
		if(BackLeft.Line == OUT)
		{
			ComeBackLinerTimer=UINT16_MAX;
			GoForwardLineAttention = 0;
			BackLineOutGoDirection = RIGHT;
		}
		else if(BackRight.Line == OUT)
		{
			ComeBackLinerTimer=UINT16_MAX;
			GoForwardLineAttention = 0;
			BackLineOutGoDirection = LEFT;
		}
	}
	else if(GoForwardLineAttention < LINE_COMEBACK_TIME)
	{
		GoForwardLineAttention++;
		if(BackLineOutGoDirection == LEFT)
			SET_RAW_MOTORS(LINE_COMEBACK_VELOCITY*0.9, LINE_COMEBACK_VELOCITY);
		else //if(BackLineOutGoDirection == LEFT)
			SET_RAW_MOTORS(LINE_COMEBACK_VELOCITY, LINE_COMEBACK_VELOCITY*0.9);
	}
	else if(FrontLeft.Line == OUT || FrontRight.Line == OUT)
	{
		ComeBackLinerTimer = 0;
		SET_RAW_MOTORS(-LINE_COMEBACK_VELOCITY,-LINE_COMEBACK_VELOCITY);
	}
	else if(FrontLeft.Distance <= MIN_LIDAR_DISTANCE && FrontRight.Distance <= MIN_LIDAR_DISTANCE)
	{
		SET_MOTORS(100,100);
	}
	else if(FrontLeft.Distance <= MAX_LIDAR_DISTANCE && FrontRight.Distance <= MAX_LIDAR_DISTANCE)
	{
		SET_MOTORS(ATTACK_STRAIGHT_ATTACK_SPEED, ATTACK_STRAIGHT_ATTACK_SPEED);
	}
	else if(FrontLeft.Distance <= MAX_LIDAR_DISTANCE && FrontRight.Distance > MAX_LIDAR_DISTANCE)
	{
		SET_MOTORS(ATTACK_STRAIGHT_ATTACK_SPEED*0.9, ATTACK_STRAIGHT_ATTACK_SPEED);
	}
	else if(FrontLeft.Distance > MAX_LIDAR_DISTANCE && FrontRight.Distance <= MAX_LIDAR_DISTANCE)
	{
		SET_MOTORS(ATTACK_STRAIGHT_ATTACK_SPEED, ATTACK_STRAIGHT_ATTACK_SPEED*0.9);
	}
	else if(lastSeen == LEFT)
	{
		SET_MOTORS(-SEARCH_STRAIGHT_ATTACK_SPEED/3, SEARCH_STRAIGHT_ATTACK_SPEED);
	}
	else if(lastSeen == RIGHT)
	{
		SET_MOTORS(SEARCH_STRAIGHT_ATTACK_SPEED, -SEARCH_STRAIGHT_ATTACK_SPEED/3);
	}
	else
	{
		SET_MOTORS(SEARCH_STRAIGHT_ATTACK_SPEED, 0);
	}
}
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

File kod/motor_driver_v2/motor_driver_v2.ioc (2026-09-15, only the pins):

Mcu.UserName=STM32H503KBUx
PA0.GPIO_Label=nFAULT_A
PA0.Signal=GPIO_Input
PA1.GPIO_Label=PWM1_B
PA1.Signal=S_TIM1_CH3
PA13(JTMS/SWDIO).Signal=DEBUG_JTMS-SWDIO
PA14(JTCK/SWCLK).Signal=DEBUG_JTCK-SWCLK
PA15(JTDI).GPIO_Label=LED3
PA15(JTDI).Signal=GPIO_Output
PA2.GPIO_Label=PWM2_B
PA2.Signal=S_TIM1_CH4
PA3.GPIO_Label=nFAULT_B
PA3.Signal=GPIO_Input
PA4.GPIO_Label=MAX_CURRENT_A
PA4.Signal=COMP_DAC11_group
PA5.GPIO_Label=MAX_CURRENT_B
PA5.Signal=COMP_DAC12_group
PA6.GPIO_Label=CURRENT_A
PA6.Signal=ADCx_INP3
PA7.GPIO_Label=CURRENT_B
PA7.Signal=ADCx_INP7
PA8.Signal=FDCAN1_RX
PA9.GPIO_Label=KILL_INPUT
PA9.Signal=GPIO_Input
PB0.GPIO_Label=VBAT
PB0.Signal=ADCx_INP9
PB1.GPIO_Label=TEMP
PB1.Signal=ADCx_INP5
PB15.Signal=FDCAN1_TX
PB3(JTDO/TRACESWO).GPIO_Label=LED2
PB3(JTDO/TRACESWO).Signal=GPIO_Output
PB4(NJTRST).GPIO_Label=LED1
PB4(NJTRST).Signal=GPIO_Output
PB6.GPIO_Label=PWM2_A
PB6.Signal=S_TIM1_CH2
PB7.GPIO_Label=PWM1_A
PB7.Signal=S_TIM1_CH1

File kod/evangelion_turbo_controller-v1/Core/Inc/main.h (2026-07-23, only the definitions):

#define START_MOD_IR1_Pin GPIO_PIN_14
#define START_MOD_IR1_GPIO_Port GPIOC
#define START_MOD_IR1_EXTI_IRQn EXTI14_IRQn
#define VBAT_Pin GPIO_PIN_4
#define VBAT_GPIO_Port GPIOA
#define LED_RED_Pin GPIO_PIN_1
#define LED_RED_GPIO_Port GPIOB
#define LED_GREEN_Pin GPIO_PIN_2
#define LED_GREEN_GPIO_Port GPIOB
#define LED_BLUE_Pin GPIO_PIN_10
#define LED_BLUE_GPIO_Port GPIOB
#define START_MOD_IR3_Pin GPIO_PIN_11
#define START_MOD_IR3_GPIO_Port GPIOB
#define START_MOD_IR3_EXTI_IRQn EXTI11_IRQn
#define JOY5_Pin GPIO_PIN_11
#define JOY5_GPIO_Port GPIOD
#define JOY4_Pin GPIO_PIN_12
#define JOY4_GPIO_Port GPIOD
#define JOY3_Pin GPIO_PIN_6
#define JOY3_GPIO_Port GPIOC
#define JOY2_Pin GPIO_PIN_7
#define JOY2_GPIO_Port GPIOC
#define JOY1_Pin GPIO_PIN_8
#define JOY1_GPIO_Port GPIOC
#define OLED_SDA_Pin GPIO_PIN_9
#define OLED_SDA_GPIO_Port GPIOC
#define OLED_SCL_Pin GPIO_PIN_8
#define OLED_SCL_GPIO_Port GPIOA
#define CAN_EN_Pin GPIO_PIN_10
#define CAN_EN_GPIO_Port GPIOA
#define CAN_RX_Pin GPIO_PIN_11
#define CAN_RX_GPIO_Port GPIOA
#define CAN_TX_Pin GPIO_PIN_12
#define CAN_TX_GPIO_Port GPIOA
#define BUZZ_PWM_Pin GPIO_PIN_4
#define BUZZ_PWM_GPIO_Port GPIOB
#define OLED_SCLB8_Pin GPIO_PIN_8
#define OLED_SCLB8_GPIO_Port GPIOB
#define OLED_SDAB9_Pin GPIO_PIN_9
#define OLED_SDAB9_GPIO_Port GPIOB
#define START_MOD_IR_2_Pin GPIO_PIN_0
#define START_MOD_IR_2_GPIO_Port GPIOE
#define START_MOD_IR_2_EXTI_IRQn EXTI0_IRQn

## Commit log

2026-03-25 tflunas + shields
    [TFMINI_S_UART.ipt, ball-bearing.0005.ipt, ball-bearing.0006.ipt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]
2026-03-25 pcb in cad interface one
    [0.96 inch oled.ipt, 0.96 oled.0002.ipt, 0.96 oled.SLDPRT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]
2026-03-27 ports from MCU done
    [ADC_low_pass_filter.SchDoc, MCU.SchDoc, Power_supply.SchDoc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]
2026-03-27 oledzik :D
    [ADC_low_pass_filter.SchDoc, OLED.SchDoc, oledzik.stp]
2026-03-28 pwr supply soft latching button with backup
    [ADC_low_pass_filter.SchDoc, Interface.SchDoc, MCU.SchDoc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]
2026-04-02 PCBiing go on
    [Interface.SchDoc, MCU.SchDoc, MotorDriver.SchDoc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]
2026-04-03 schematics for PCB controller done
    [BTB_Main_connector..SchDoc, BTB_Top_connector.SchDoc, Buzzer.SchDoc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]
2026-04-03 Schematics done
    [BTB_Main_connector..SchDoc, BTB_Main_connector.SchDoc, BTB_Top_connector.SchDoc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]
2026-04-04 THIS LOOCK SO FCKING COOL - pcb new sizeing
    [2s450mah.ipt, BearigHold.0002.ipt, BearigHoldLeft.0004.ipt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]
2026-04-05 slight redesign. i thhink 3d model is doen
    [Atiumik_interface.dwg, Atiumik_interface.ipt, BTB_Main_connector.SchDoc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]
2026-04-07 front i płóg zrobiony
    [3s450mah.0004.ipt, 3s450mah.0005.ipt, 3s450mah.ipt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]
2026-04-07 something 3d model done done done
    [Ceiling.0016.ipt, Ceiling.ipt, FonrtMount.0111.ipt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]
2026-04-07 i think 3d model is mainly done. we can do PCBs now!
    [Ceiling.0016.ipt, Ceiling.0018.ipt, Ceiling.ipt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]
2026-04-08 pcb sheets no motors to interface connector fix
    [ADC_low_pass_filter.SchDoc, BTB_Main_connector..SchDoc, BTB_Main_connector.SchDoc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]
2026-04-09 front steel sheet
    [FonrtMount.0139.ipt, FonrtMount.0140.ipt, FonrtMount.ipt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]
2026-04-09 3d model to prinring now?
    [FonrtMount.0140.ipt, FonrtMount.0142.ipt, FonrtMount.ipt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]
2026-04-11 SpringSteelFront gerbers
    [SpringSteelFront.PcbDoc, SpringSteelFront.stp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]
2026-04-13 new left hearbox
    [BearigHoldLeft.0028.ipt, BearigHoldLeft.0029.ipt, BearigHoldLeft.ipt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]
2026-04-14 left gearbox
    [LeftGearbox.0018.ipt, LeftGearbox.0025.ipt, LeftGearbox.ipt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]
2026-04-14 R and L gearbox covers
    [LeftGearboxCoverr.0005.ipt, LeftGearboxCoverr.0007.ipt, LeftGearboxCoverr.ipt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]
2026-04-14 pcbs mount
    [GearboxBearingHolderCover.0005.ipt, GearboxBearingHolderCover.ipt, GearboxBearingHolderCover_MIR.ipt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]
2026-04-14 pcb in work
    [Connectors.SchDoc, Interface.SchDoc, OledAndLed.SchDoc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]
2026-04-15 rules and interface
    [Connectors.SchDoc, OledAndLed.SchDoc, PCB_Interface.PcbDoc]
2026-04-16 motors calculation sheet
    [SilniczkiExcel.xlsx]
2026-04-17 added fan into function
    [1703 Fan asm.STEP, 1703 Fan asm.ipt, PCB_Main.0003.ipt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]
2026-04-17 MY CHONKERS ARE HEREEE
    [ADC_low_pass_filter.SchDoc, BTB_Main_connector.SchDoc, BTB_Top_connector.SchDoc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]
2026-04-21 pcb motors
    [DiyHub.0014.ipt, DiyHub.0029.ipt, DiyHub.ipt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]
2026-04-22 motor driver pcb
    [Interface.SchDoc, MCU.SchDoc, MotorDriver.SchDoc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]
2026-04-26 3dp v2
    [DiyHub.0029.ipt, DiyHub.0030.ipt, DiyHub.ipt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]
2026-04-26 i frog...
    [DiyHub.stp]
2026-04-27 MotorsPCB big update
    [FonrtMount.stp, LeftGearboxCoverr.0054.ipt, LeftGearboxCoverr.0055.ipt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]
2026-04-28 motor drivers in cad
    [PCB_Motors.0005.ipt, PCB_Motors.PcbDoc, PCB_Motors.ipt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]
2026-05-03 Files recovered succesfully from my broken laptop
    THANK GOD. I managed to recover files from my broken laptop, Idk why i dint have them on repo...
    [BOM.xlsx, Koszta.xlsx, SilniczkiExcel.xlsx]
2026-05-03 testing and assembly of the prototpye
    [BOM.xlsx]
2026-05-03 motor driver from scratch and 3dp parts update and fixes, features
    [3s450mah.0006.ipt, 3s450mah.0011.ipt, 3s450mah.ipt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]
2026-05-04 C0 in driver instead of G431
    [Interface.SchDoc, LunasCover.0004.ipt, LunasCover.0006.ipt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]
2026-05-04 motor driver update - rethinking about galvanic isolation
    [BOM.xlsx, Interface.SchDoc, MCU.SchDoc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]
2026-05-07 github? Github? are you there?
    [0.96 oled.0002.ipt, 0.96 oled.0003.ipt, 0.96 oled.ipt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]
2026-05-07 u0pdate of photos of motor driver at main page
2026-05-09 general update + buzzer + more IR receivers
    [Buzzer.SchDoc, Connectors.SchDoc, External_ir_receiver.SchDoc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]
2026-05-11 updateo, pcb working in working! 1/2
    [DiyHub.stp, FonrtMount.stp, GearboxBearingHolderCover.stp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]
2026-05-11 updateo, pcb working in working! 2/3
    [IMU.SchDoc, MCU.SchDoc, PCB_INTERFACE.SchDoc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]
2026-05-11 updateo, pcb working in working! 3/3
    [Interface_assembly.iam, LeftGearbox.0105.ipt, LeftGearbox.0107.ipt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]
2026-05-12 pcb may be okay!
    [DiyHub.stp, Felga.stp, FonrtMount.stp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]
2026-05-12 fix for plating
    [Buzzer.SchDoc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]
2026-05-14 image fix
    [main.1362.iam, main.1363.iam, main.iam]
2026-05-27 bom bom bim bom

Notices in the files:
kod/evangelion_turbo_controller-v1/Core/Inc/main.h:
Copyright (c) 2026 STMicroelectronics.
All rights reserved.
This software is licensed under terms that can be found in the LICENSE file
